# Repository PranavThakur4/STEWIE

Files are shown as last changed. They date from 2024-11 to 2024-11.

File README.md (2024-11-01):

# STEWIE
 Theuseofparallelmanipulatorsinaerospaceengineeringhasgainedsignificantattentiondueto
 their ability to provide improved stability and precision. This paper presents the design, control, and analysis
 of “STEWIE”,whichisathree-degree-of-freedom(DoF)parallel manipulator robot developed by members
 of the thrustMIT rocketry team, as a payload stabilization mechanism for their sounding rocket, ’Altair’. The
 goal of the robot was to demonstrate the attitude control of the parallel plate against the continuous change
 in orientation experienced by the rocket during its flight, stabilizing the payloads. At the same time, the high
 gravitational forces (G-forces) and vibrations experienced by the sounding rocket are counteracted. A novel
 design of the mechanism, inspired by a standard Stewart platform, is proposed which was down-scaled to
 fit inside a 4U CubeSat within its space constraints. The robot uses three micro servo motors to actuate the
 links that control the alignment of the parallel plate. In addition to the actuation mechanism, a robust control
 system for its manipulation was developed for the robot. The robot represents a significant advancement
 in the field of space robotics in the aerospace industry by demonstrating the successful implementation of
 complex robotic mechanisms in small, confined spaces such as CubeSats, which are standard form factors
 for large payloads in the aerospace industry.

 Stewie Payload
 STEWIE Cubesat 4U

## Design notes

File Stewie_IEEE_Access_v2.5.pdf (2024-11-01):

Date of publication xxxx 00, 0000, date of current version xxxx 00, 0000.

Digital Object Identifier 10.1109/ACCESS.2023.0322000

# Design and control of "STEWIE", a robotic payload stabilization mechanism for rocket flights

Utkarsh Anand¹* | Diya Parekh²* | Thakur Pranav G. Singh³* | Hrishikesh S. Yadav⁴
| Ramya S.
Moorthy⁵

| Srinivas G.⁶

1Department of Electrical & Electronics Engg., Manipal Institute of Technology, Karnataka, India - 576104 (email: utkarshanan221@gmail.com) 2Department of Mechatronics Engg., Manipal Institute of Technology, Karnataka, India - 576104 (email:diyaparekh0603@gmail.com) 3Department of Mechanical Engg., Manipal Institute of Technology, Karnataka, India - 576104 (email:thakur4pranav@gmail.com)
4Department of Data Science Engg., Manipal Institute of Technology, Karnataka, India - 576104 (email: yadavhrishikeshsingh@gmail.com) 5Department of Mechatronics Engg., Manipal Institute of Technology, Karnataka, India - 576104 (email: ramya.moorthy@manipal.edu) 6Department of Aeronautical & Automobile Engg., Manipal Institute of Technology, Karnataka, India - 576104 (email:srinivas.g@manipal.edu)

Corresponding author: Srinivas G. (e-mail: srinivas.g@manipal.edu).

*These authors share equal contribution
Project funded by Manipal Academy of Higher Education (MAHE) and undertaken by authors as members of thrustMIT Rocketry Team.

ABSTRACT The use of parallel manipulators in aerospace engineering has gained significant attention due to their ability to provide improved stability and precision. This paper presents the design, control, and analysis of “ STEWIE ”, which is a three-degree-of-freedom (DoF) parallel manipulator robot developed by members of the thrustMIT rocketry team, as a payload stabilization mechanism for their sounding rocket, ’Altair’. The goal of the robot was to demonstrate the attitude control of the parallel plate against the continuous change in orientation experienced by the rocket during its flight, stabilizing the payloads. At the same time, the high gravitational forces (G-forces) and vibrations experienced by the sounding rocket are counteracted. A novel design of the mechanism, inspired by a standard Stewart platform, is proposed which was down-scaled to fit inside a 4U CubeSat within its space constraints. The robot uses three micro servo motors to actuate the links that control the alignment of the parallel plate. In addition to the actuation mechanism, a robust control system for its manipulation was developed for the robot. The robot represents a significant advancement in the field of space robotics in the aerospace industry by demonstrating the successful implementation of complex robotic mechanisms in small, confined spaces such as CubeSats, which are standard form factors for large payloads in the aerospace industry.

INDEX TERMS Parallel Manipulators, Robotics, Payload, Sounding Rocket, Control Systems, Kinematics

I. INTRODUCTION
T

HE successful use of payloads in space missions depends largely on ensuring their stability and orientation control during the launch and spaceflight phases. Vibration motion, G-forces and dynamic disturbances caused by the rocket’s orientation during flight path can affect the integrity and functionality of the payload. To address these challenges, parallel manipulators have emerged as a promising solution, offering the potential to counteract these external perturbations and maintain precise alignment.
The inspiration for the design of our robot STEWIE comes from the versatility and robustness of the six degrees-of-freedom (DoF) Stewart platform, which is widely used in various industrial and research applications. Our research aims to take advantage of the principles of the Stewart platform while simplifying the kinematic structure to create a three-degrees-of-freedom (DoF) parallel manipulator suitable for payload stabilization in thrustMIT’s sounding rocket: Altair.
The main goal of this article is to present a comprehensive study of STEWIE’s design, development and performance characteristics. We address the kinematic analysis of the manipulator and illustrate its ability to provide three degrees-of-freedom for precise positioning of the payload during rocket ascent and spaceflight. In addition, we are investigating the integration of different types of joints and micro-servo motors into STEWIE’s structure to improve its parallel alignment with respect to the Earth’s surface. We present the results of the various structural simulations carried out on STEWIE to ensure that it can function effectively in the harsh conditions it will experience during its flight inside the rocket.
We also propose a computationally in-expensive but robust controller which has high response speeds and high movement accuracy.
The research results show that STEWIE has exceptional
VOLUME 11, 2023 | 1

Author et al.: Preparation of Papers for IEEE TRANSACTIONS and JOURNALS

potential as an effective payload stabilization system for sounding rockets such as Altair. The ability of the manipulator to actively counteract vibrational movements, G-forces and orientation changes ensures the integrity and reliable functionality of payloads during critical phases of space missions. Furthermore, its compact, lightweight and simple design contributes to the rocket’s overall efficiency and improved payload capacity.

A. CONTRIBUTIONS OF RESEARCH
The main contributions of this paper to the field of robotics and aerospace are the following:-
- A novel low-complexity, pwm-controlled actuator based payload stabilization mechanism for rocket flights.
- A computationally lightweight controller, demonstrating high accuracy and response time for critical robotic application especially in space industries.
- A simple and robust custom tuning method for pidcontrollers.
- An open-source platform comprising mechanical design files (STEP format), details of electronic components, and real-time-operating-system (RTOS).
B. ORANISATION OF PAPER
The paper is organized as follows: a comprehensive study on related work and recent development in the the field of robotics, especially for aerospace applications and in payloads has been presented in section II. The design of the robot detailing its geometry, kinematics involved, various components used, actuation mechanism, along with communication interfaces, sensors and circuitry design are described in section III. A detailed description of the control architecture including the controllers used, are explained in section IV. A comprehensive description of the tuning methods for the controllers is given in section V. Analysis of the simulations, and actual rocket flight results are presented in section VI. Finally, we present our conclusion in section VII.

II. RELATED WORK & RECENT DEVELOPMENTS
The utilization of Stewart platforms in aerospace applications has seen a surge in interest owing to their capability to provide precise control and stabilization in dynamic environments. Recent advancements in this field have seen various applications ranging from vibration control systems to robotic manipulators designed specifically for space missions. This section reviews significant advancements in the fields of robotics, Stewart platforms, and their application within the aerospace industry, focusing on the stabilization of payloads during rocket flights.
Stewart platforms, first introduced by Eric V. Gough (1947)
[2] and D.Stewart et al. (1965) [1] are known for their high stiffness, force capabilities, and precise motion control and have been increasingly employed in aerospace applications to address challenges related to maintaining orientation and stability in dynamic environments. Research by Tsai et al. (1999) [3] and Melek et al. (2010) [4] have highlighted the mechanics and kinematics of Stewart platforms, emphasizing their suitability for tasks requiring high precision and complex motion control.
Wang et al. (2022) [7] explored the utilization of Stewart platforms in the low-frequency vibration characteristic testing of space truss deployable antennas mounted on satellites. Their study demonstrated the effectiveness of Stewart platforms in conducting vibration tests, crucial for assessing the structural integrity and performance of satellite components in space environments.
Preumont et al. (2007) [6] presented a pioneering work on a six-axis single-stage active vibration isolator based on a Stewart platform. This work introduced a novel approach to mitigating vibrations in aerospace systems, which is essential for improving the accuracy and reliability of sensitive instruments and payloads onboard spacecraft.
Liang et al. (2021) [5] contributed to the field with their research on the design and implementation of a high-precision Stewart platform tailored for a space camera. Their study focused on achieving precise positioning and stabilization of the camera platform, crucial for capturing high-quality images and conducting remote sensing operations in space. In a related study, Liang et al. (2022) conducted kinematics and dynamics simulations of a Stewart platform, providing valuable insights into its motion characteristics and performance metrics.
Furthermore, Glassner (2021) explored the concept of soft Stewart platforms tailored for robotic in-space assembly applications. This innovative approach introduces flexibility into the platform structure, enabling adaptability to varying task requirements and enhancing safety during assembly operations in space environments.
These works collectively highlight the diverse applications and recent advancements in Stewart platform technology within the aerospace industry. The versatility, precision, and adaptability of Stewart platforms make them indispensable for a wide range of aerospace missions, including satellite deployment, vibration control, payload stabilization, and in-space assembly operations.

III. ROBOT DESIGN
In this section we will discuss in detail the overall geometry of the mechanical structure, the forward kinematic calculations for the robot, the computing & communication implemented, finally focusing on the leg design and the actuation mechanism of the robot.
A. GEOMETRY OF ROBOT
The hardware design of STEWIE is inspired from a Stewart-Gough Platform [1]. The design philosophy behind the mechanism is based on compactness, light weight construction, ease of manufacturing, rapid repair and robust operation. The design of the robot can be understood as an assembly of three sections, stationary base & middle plates, 3 identical custom designed legs and a dynamic top plate where the payload to be stabilized sits (refer Fig. 1). STEWIE weighs
2 | VOLUME 11, 2023

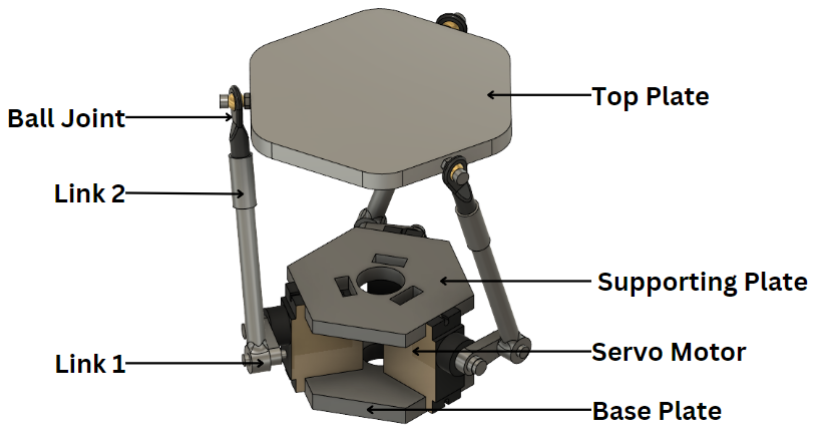
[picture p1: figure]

FIGURE 1. Computer Aided Design (CAD) of STEWIE Robot

TABLE 1. Physical Robot Parameters

Parameter | Symbol | Value | Units
Mass | m | 485 | g
Minimum Body Height | lbody | 110 | mm
Maximum Body Height | lbody | 125 | mm
Body Width | wbody | 85 | mm
Leg Link Length | l1, l2, l3 | 79 | mm
Maximum Load Capacity | - | 10.91 | kg-f

around 485 g with a maximum height of 125 mm, when fully extended and minimum height of 110 m, from ground to top plate depending on the positions of the legs. Each leg of the robot measures a total length of 79 mm and has a maximum load capacity of 10.91 kg − f .

Degrees of Freedom
The degrees-of-freedom of STEWIE were calculated using Chebychev–Grübler–Kutzbach criterion:

FT = 6(N − 1 − J) +X(Fi
- Ji) | (1)

Where,
N : Number of links = 8
J : Number of joints = 9
Fi

: Degrees of Freedom of a joint
Ji

: Number of joints with the same degree-of-freedom

Here, the summation term of (1) represents the effective constraints which are acting on the robot. In STEWIE, six revolute joints with one-degree-of-freedom and three ball joints with three-degrees-of-freedom each have been used. Hence, the summation term of (1) can be calculated as follows:

X(Fi · Ji) = (1 · 6) + (3 · 3) = 15

Therefore, on substituting the given values in the criterion given in (1), degrees-of-freedom calculated for STEWIE is calculated as FT = 3.

B. COMPUTING AND COMMUNICATION
The robot was deployed inside a CubeSat, which was divided into two segments. The upper segment houses the robot along with two first-person-view (FPV) cameras to record the movement of the plates during the rocket flight from two

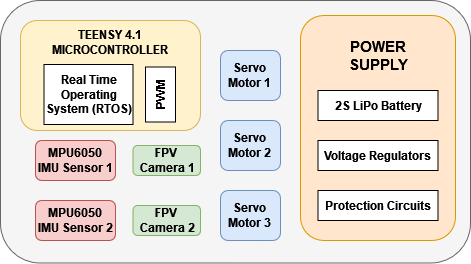
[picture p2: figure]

FIGURE 2. Electronics System Block Diagram

different angles. For inertial measurement, a small printedcircuit-board (PCB) is mounted on the top plate of the robot which has a MPU6050 inertial-measurement-unit (IMU) on it for orientation data of the plate. A secondary IMU is mounted on the bottom plate of the robot, which remains stationary with respect to the frame of reference of the rocket during its flight. This secondary IMU helps to determine the orientation of the top plate in reference to the rocket’s frame of reference. The bottom segment consists of majority of the electronics components, cable routing and two power distribution boards each for the two cameras. The power is supplied to the parallel manipulator robot through an extension from a 2S Lithium-Polymer (LiPo) battery with additional batteries for redundancy. The central processing unit of the robot is a Teensy 4.1 microcontroller, functioning on a FreeRTOS based real-timeoperating-system (RTOS). The processor communicates with the IMU sensor daughter boards through high-speed Inter-Integrated-Circuit (I2C) interface with each IMU sensor on a different address. The servo motors are controlled by the microcontroller via pulse-width-modulated (PWM) signals generated by it (refer Fig. 2). This setup executes control strategies, including control of motors at frequencies as high as 200 Hz.

C. LEG DESIGN & ACTUATION
The robot comprises of three legs. Each leg of the robot is divided into three sections. The bottom section of the leg is a revolute joint which comprises a micro-servo motor placed at the base of each leg and a link-1 (refer Fig. 3) which connects the motors to the middle section of the leg. Link-1 is connected to the middle section of the leg through a nutbolt mechanism, which acts as the second revolute joint. The middle section of the robot is a cylindrical rod which we call as Link-2 (refer Fig. 3). The top section of the leg comprises of a ball joint which connects the leg to the top plate of the robot. The motors are attached and sandwiched between the middle and the base plate of the robot to prevent them from moving during the actuation of the robot. The motor acts as the driver for the actuator and the joints above are driven by it, translating the motor’s rotary motion into linear and angular displacement of the top plate. Each leg of the robot measures a total length of 79 mm and weights around 26 g.

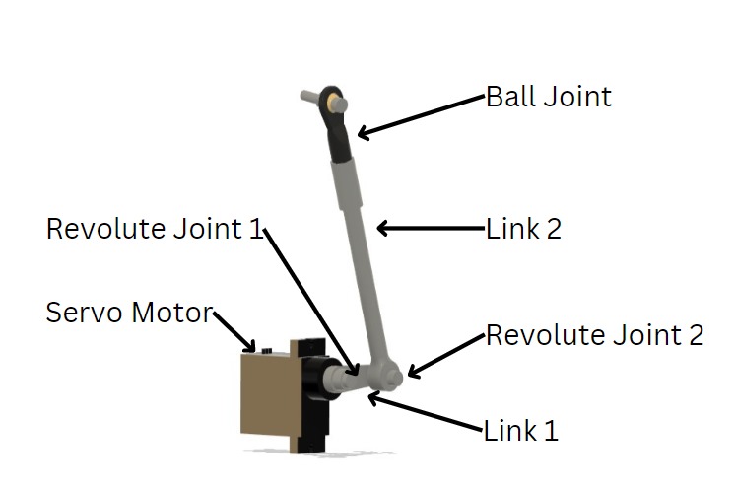
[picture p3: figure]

FIGURE 3. Leg Design of Robot

During development of the robot, other potential methods of actuation were also explored such as pneumatic actuators, linear actuators in its early iterations. Though effective, but these early iterations were rejected due to unavailability of cost effective commercial actuators and space constraints inside the CubeSat.

TABLE 2. Specification of Components of Robot

Part | Material | Weight | Units
Top Plate | ABS Plastic | 53 | g
Middle Plate | Steel | 105 | g
Base Plate | Steel | 85 | g
Link 1 | Aluminium 6061 | 13 | g
Link 2 | Aluminium 6061 | 4 | g
Ball Joint | Plastic | 3 | g

TABLE 3. Micro Servo Motor Specifications

Parameter | Value | Units
Model | SG-90
Mass | 9.0 | g
Motor Size | 22.2 | mm
| 11.8 | mm
Operating Speed | 0.1 | s/60 degree
Operating Voltage | 4.8 | V
Maximum Torque | 2.5 | Kg-cm

IV. CONTROL ARCHITECTURE
Our control architecture follows a combination of a custom robot state estimator which analyzes the orientation of the robot’s top plate along the {X, Y , Z} axes and performs forward kinematic calculations to determine the position matrix of the ball joints in the form of cartesian coordinates in the three-dimensional space, which is then passed as an input to three separate low-level controllers for each of the three legs (refer Fig. 6). The controllers generates the motor angles for each motor, by which the it should move to ensure that the top plate is parallel to the ground no matter the orientation of the

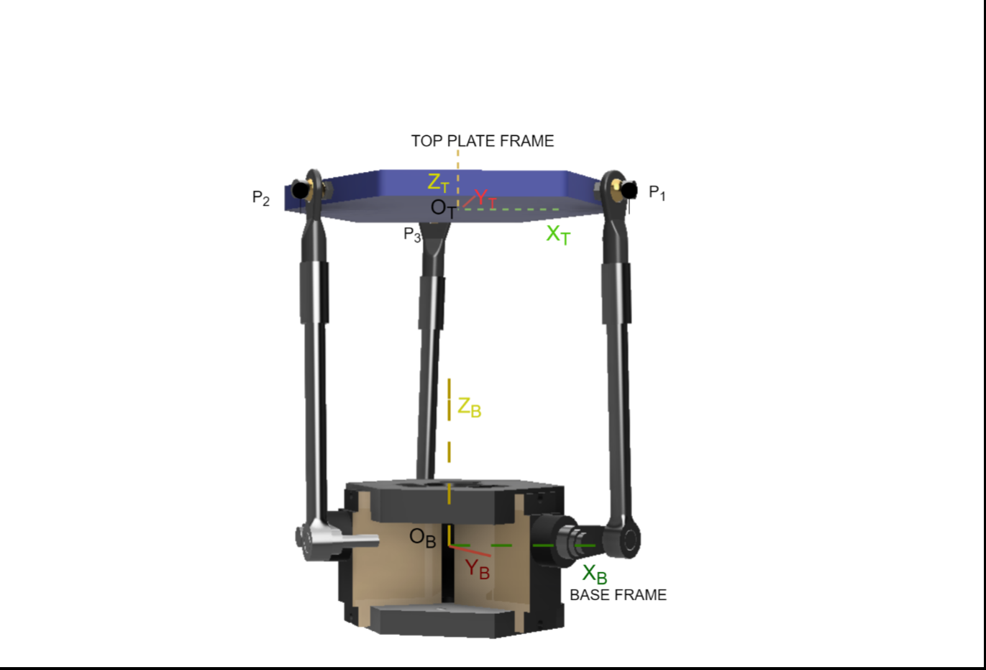
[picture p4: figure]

FIGURE 4. Frame of References in Robot

robot or the rocket. This in-turn stabilizes the payload which is kept on the robot.
This control approach allows for a decoupling of the control process, simplifying the design and implementation.
A. ROBOT STATE ESTIMATOR
Robot’s State: The state of the robot at any given time, is a three-dimensional vector St = {Xp, Yp, Zp} consisting of the position coordinates of the ball joints with respect to the the base frame (refer Fig. 4) along the X, Y & Z axis at which the legs are connected to the plate through the ball joints. Forward Kinematic calculations were done on the robot to determine the final position matrix of the ball joints. The IMU sensor which is attached to the top plate of the robot has a three-axis gyroscope and can give orientation data of the top plate in the form of angle deviations from three axes as known as Yaw, Pitch and Roll. This information was utilized to calculate the position of ball joints in the base frame. Here, the ’base frame’ is defined as the initial frame located at the centre of the three motors (refer Fig. 4). The base frame is at a fixed distance from the frame of reference of the top plate throughout the flight irrespective of the position of the motors. Position matrix of top plate with-respect-to base plate frame of the robot was presented as BTT , where, {θX , θY , θZ } are the angle deviations of the top plate along from the X, Y , Z axes obtained from the Yaw-Pitch-Roll data from the IMU and BZT is the fixed distance between the top plate frame and base frame. The position matrix of ball joint with respect to top plate frame was represented as T TP, where, {x, y,z} are the coordinates of the ball joints in the three-dimensional space in the frame of reference of the top plate.
To find position matrix of ball joint with respect to base frame, BTT and T TP were multiplied.

BTP =

T TP ·

BTT | (2)

Refer to Fig. 5 for detailed matrix multiplications.

TTP =

1 0 0 x
0 1 0 y
0 0 1 z
0 0 0 1

BTT =

cos θZ · cos θY | − sin θZ · cos θX + cos θZ · sin θY · sin θX | sin θZ · sin θX + cos θZ · sin θY · cos θX | 0
sin θZ · cos θY | cos θZ · cos θX + sin θZ · sin θY · sin θX | − cos θZ · sin θX + sin θZ · sin θY · cos θX | 0
− sin θY | cos θY · sin θX | cos θY · cos θX | BZT
0 | 0 | 0 | 1

BTP =

cos θZ · cos θY | − sin θZ · cos θX + cos θZ · sin θY · sin θX | sin θZ · sin θX + cos θZ · sin θY · cos θX | Xp
sin θZ · cos θY | cos θZ · cos θX + sin θZ · sin θY · sin θX | − cos θZ · sin θX + sin θZ · sin θY · cos θX | Yp
− sin θY | cos θY · sin θX | cos θY · cos θX | Zp
0 | 0 | 0 | 1

FIGURE 5. Position Matrices of Robot

Where,
Xp = (cos θZ · cos θY ) · x + (− sin θZ · cos θX + cos θZ · sin θY · sin θX ) · y + (sin θZ · sin θX + cos θZ · sin θY · cos θX ) · z Yp = (sin θZ · cos θY ) · x + (cos θZ · cos θX + sin θZ · sin θY · sin θX ) · y + (− cos θZ · sin θX + sin θZ · sin θY · cos θX ) · z Zp = (− sin θY ) · x + (cos θY · sin θX ) · y + (cos θY · cos θX ) · z + Z

B
T

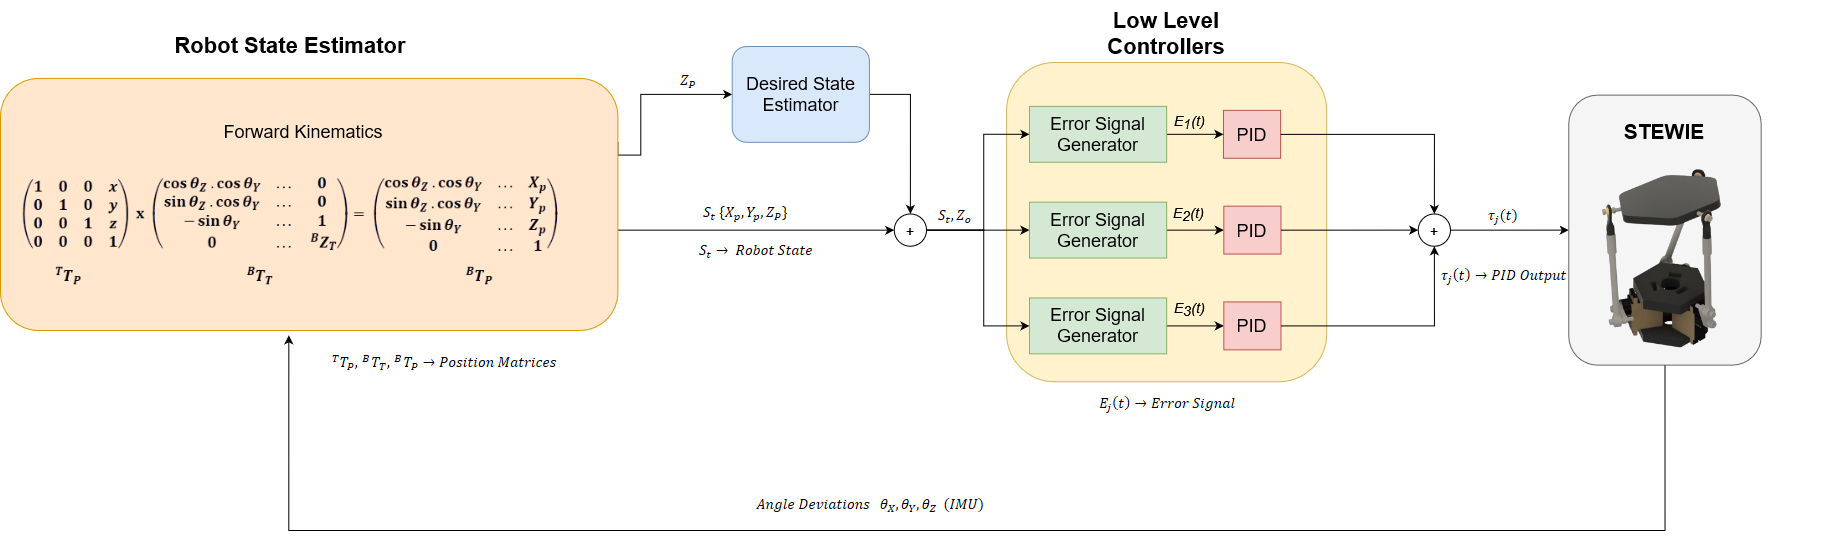
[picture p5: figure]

FIGURE 6. Control Architecture

B. LOW LEVEL CONTROLLER

Approaching the robot’s locomotion challenge from a control theory perspective, we aim to develop a policy capable of parameterizing the relationship between the angular positions of the servo motors and the orientation of robot’s top plate in the three-dimensional space furthermore analyzing how changing the angular position of the servo changes the orientation of the top plate. These parameterized value act as inputs for the controllers, which, in turn, incorporates a regulatory mechanism based on the orientation state of each leg.

Desired State: The desired state of the robot is one in which the top plate should be parallel to the ground. In our case, when the top plate is parallel to the ground, it is in absolute horizontal orientation with respect to the ground surface and at that instance, the z−coordinate of all the ball joints are same. Therefore, the controller will be regulating the motors such that their z−coordinate of all the motors are same to achieve horizontal orientation of the top plate with respect to ground.

Error Signal: At any given state, the errors signal (Ej) for the three controllers are calculated by taking the absolute difference between between the desired z-coordinate, Zo, also known as set-point (SP) and the actual z-coordinates of the three points of the ball joints, Zp1

, Zp2

, Zp3
, also known as
process-variables (PV) in control theory.

Ej = |Zo − Zpj

| ∀ j = 1, 2, 3 | (3)

The desired z-coordinate (Zo) for the controller is chosen as the median of the actual z-coordinates of the three ball joints.

Zo = median{Zp1
, Zp2

, Zp3

} | (4)

This also reduces the computational complexity of the model as, at given state, controller calculations for only two of three motors have to be done because the leg having the median z-coordinate will remain stationary.
The motor level controllers tracks the z-coordinates of the plate points at every time instant ’t’ using a Proportional-Integral-Derivative (PID) controller with appropriate gains Kp, Ki

, and Kd for each of the three controllers as follows:

τj(t) = Kpj

- Ej(t) + Kij

·

Xt−1

k=0

Ej(k) + Kd · E˙
j(t)

∀ j = 1, 2, 3 (5)

Where,
τtj
: PID output of the j

th controller at time instant t. Etj

: Error of the j

th controller at time instant t. Ref. (3) Kpj

: Proportional gain of the j

th controller.
Kij

: Integral gain of the j

th controller.
Kdj

: Derivative gain of the j

th controller.

V. TUNING OF CONTROLLERS
The effective tuning of PID controllers is crucial for achieving optimal performance in robotic system, particularly those with complex dynamics such as parallel manipulators. In this section, we will discuss the methods employed for tuning the PID controllers. We utilized three different methods: a custom tuning method and two heuristic tuning methods, Ziegler-Nicholas, proposed by J.G. Ziegler & N.B. Nicholas (1942)
[13] and the Cohen-Coon Method, proposed by G.H. Cohen and G.A. Coon (1953) [14].
In all the methods, to get system response signal, the process-variable which are the z-coordinates Zp1

, Zp2

, Zp3
for
the three ball joints and set-point, which is the desired z-coordinate Zo; were plotted against time t. Final values of PID gains were chosen based on the comparison results of the different methods.
A. CUSTOM TUNING METHOD
This method was an modified version of the trial-error method of tuning a controller. The method involved performing open-loop test on the controller to determine the process characteristics of the controller followed by manually adjusting the gains depending on the results of the open-loop test. We used a random value of the set-point during each iteration as the reference signal.
The process involved following steps:
1) Perform Open-loop Test
The controllers were configured in manual mode and a stepchange was introduced as the output signal. The process-variable (PV) curve response was monitored continuously and it was determine the that controller gave a self-regulating characteristic with pure 1

st order lag. Hence, it was inferred that the proportional gain was dominant for the controller had to be aggressive along with a nominal integral gain. The derivative gain could be used or avoided depending on the results in the future.

2) Manually Adjusting Gains
After recognising the characteristics of the controller, the gains were initialized with values of Kp & Ki = 0.5 and Kd = 0. Post initialization, they are manually adjusted based on rules given in Table 4 to achieve the best compromise between stability and quick response of the system.
B. ZIEGLER-NICHOLS METHOD (CLOSED LOOP) Ziegler-Nicholas closed-loop is a heuristic method for tuning controllers in which certain parameters of the system such as Ultimate Gain (Ku) and Critical Period (τu) are determined manually through experimentation. Following which, the Kp, Ki

, Kd gains can be calculated through pre-determined rules based on the ultimate gain and the critical period given in Table 5.

TABLE 5. Ziegler-Nicholas Method Tuning Rule

Gain Type | Kp | Ti | Ki | Td | Kd
P | Ku/2 | - | - | - | -
PI | Ku/2.2 | τu/1.2 | Kp/Ti | - | -
PID | Ku/1.7 | τu/2 | Kp/Ti | τu/8 | Kp ∗ Td

The process involved the following steps:
Step 1 : Keeping the integral gain (Ki) and derivative gain (Kd ) as zero, proportional gain (Kp) is increased until the system starts to oscillate continuously at a constant amplitude. The gain at this point is called the Ultimate Gain (Ku). The calculated values of ultimate gains for the three controllers is given in Table 6.
Step 2 : Critical Period (τu) is determined by measuring the period of oscillation at the ultimate gain. The calculated values of critical periods for the three controllers is given in Table 6.
Step 3 : Using a set of pre-defined formulas presented by Ziegler-Nicholas given in Table 5, the values of

TABLE 4. General rule for tuning control parameters

Parameter | Rise Time | Overshoot | Settling Time | Steady-State Error
Kp | Decrease | Increase | Minor Change | Decrease
Ki | Decrease | Increase | Increase | Eliminate
Kd | Minor Change | Decrease | Decrease | Minor Change

Kp, Ki

, Kd gain were calculated. Final values of the gains are given in Table 6.

TABLE 6. Gains calculated through Ziegler-Nicholas Method

Type of Controller | Ku | τu | Kp | Ti | Td
Leg 1 PID Controller | 6.63 | 0.24 | 3.98 | 0.12 | 0.03
Leg 2 PID Controller | 4.65 | 0.24 | 2.79 | 0.10 | 0.03
Leg 3 PID Controller | 7.92 | 0.16 | 4.75 | 0.08 | 0.02
C. COHEN-COON METHOD
Cohen-Coon method is an extension of the Ziegler-Nicholas Method, but uses more information from the system in the process. The system’s response is modelled to a step change as a first-order response plus dead time using this method. From the response, three parameters: K, τm and τd are founded. K is the output steady state divided by the input step change, τm is the effective time constant of the first-order response, and τd is the dead time.

τm =

3
2
(t2 − t1) | (6)
τd = t2 − τm | (7)

To verify the results, according the Cohen Coon rules, the dead time should be less than two times the length of the time constant [1]. The Cohen Coon relations for calculating the PID gains is given in Table 7.

TABLE 7. Cohen-Coon Method Tuning Relations

Type of Controller | Kp | Ti | Td
P | τm (1 + τd ) Kτd 3τm | - | -
PI | τm (0.9 + τd ) Kτd 12τm | 30+3τd/τm τd ( ) 9+20τd/τm | -
PD | τm (1.25 + τd ) Kτd 6τm | - | 6−2τd/τm τd ( ) 22+3τd/τm
PID | (1 + τd τm ) Kτd 3τm | 32+6τd/τm τd ( ) 13+8τd/τm | τd ( 4 ) 11+2τd/τm

The obtained system parameters and calculated systems gains are given in Table 8.

TABLE 8. System parameters calculated through Cohen-Coon Method

Controller | K | τd | τm | Kp | Ti | Td
Leg 1 PID Controller | 2.9 | 0.07 | 0.47 | 2.85 | 0.43 | 0.08
Leg 2 PID Controller | 3.92 | 0.03 | 0.37 | 2.15 | 0.25 | 0.06
Leg 3 PID Controller | 1.71 | 0.05 | 0.55 | 4.58 | 0.55 | 0.05

The system response curves for tuning PID controllers using the above given methods is given in Fig. 7.

VI. RESULTS & DISCUSSIONS
A. SIMULATIONS
1) Modal Analysis
Necessary modal analysis simulation was performed on the robot to observe its behaviour under high vibrational forces. The formations and stress zones were identified at different natural frequencies and accordingly the design of the robot was also modified to provide more support in high stress areas. Based on the analysis, the robot was finally designed to sustain a maximum of 16 G-forces under continuous orientation change during the rocket flight.
The simulations were performed for five mode shape results for a total deformation. As expected, the maximum stress was found to be at the joints in the link-2 and the ball joint as they were externally joined by a transition fit but sufficient length was not present to hold on. Stress regions were also observed at the sharp edges of the top plate and the link-2, which weren’t filleted to reduce stress concentration. However, the edges were filled and filleted later to least possible diameter to justify the stress concentration. The maximum total deformation observed was 261.57 mm at a frequency of 761.13 Hz. Since, the natural frequency of the rocket during its flight was between 70 - 100 Hz, we were in a safe zone with a decent amount of factor of safety.
2) Static Structural Simulation
It was necessary to perform static structural simulations on the robot to observe the effects of downward acting load on the robot, experienced during the rocket flight. To carry out the simulations, the 3D CAD model was imported into the Ansys software as a STEP file. Appropriate materials were assigned to the respective parts of the robot and the

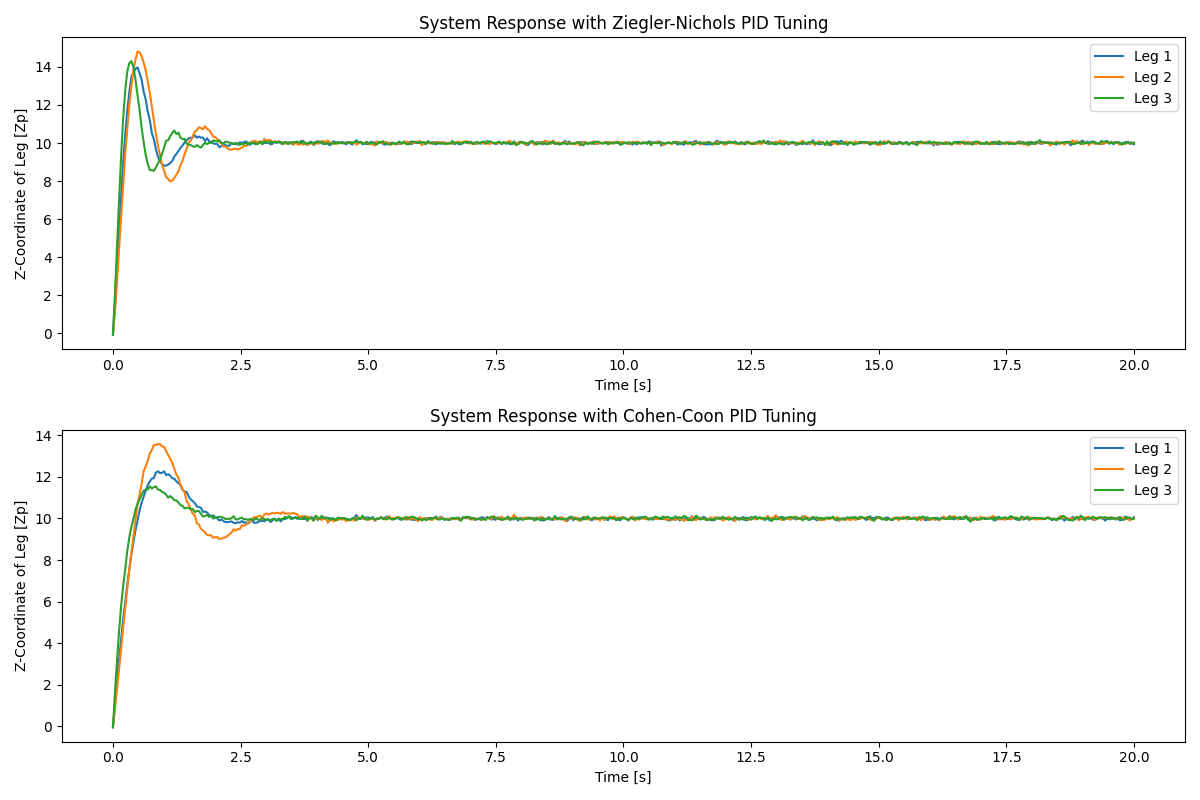
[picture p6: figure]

FIGURE 7. System Response Curves for PID Controllers with desired Zo = 10

necessary regions were given the property of contact regions bonded with no separation. To define the threads region, local coordinate system was assigned to the center of the bolts. Further, meshing was performed to the model, which was a combination of Tet and Hex mesh elements. The regions where the load effects were anticipated to be higher like the links, Hex mesh was assigned to such regions for accurate results and the regions where the loads were anticipated to be lesser, Tet mesh was assigned to reduce overall complexity and compute time of the simulation. There were a total of 0.25 million elements in quadratic order with a size of 0.75 mm.
The force applied to the simulation was calculated as following:- The maximum torque which can be delivered by the servo motor was 10g/cm or 1kg/m. The length of each link was 15 mm, hence through simple torque calculation, the maximum force on each link was 66.66 N in the ideal condition. Considering losses and practical efficiency of 85% for the motors, the maximum force on each link can be calculated as 56N or 5.6Kg. Adding a factor of safety of 1.5 for maximum load, each link could lift a maximum weight of 3.8Kgs, therefore making it 11.4Kgs for the whole robot which converts to approximately, 107N.
During the rocket’s flight, the maximum downward G-forces acting on the rocket was 12G’s which is equivalent to 117N. Majority of this downward force is experienced by the frame and the structure of the rocket body namely the stringers and the bulkheads. The payload is also protected by its own supporting plates and the walls of the CubeSat. Thus, the net effect of these downward forces acting on the payload is significantly reduced, approximately up to 50% of its original value.

Therefore, final value of the G-force acting on the payload is considered as 59N. The weight of the top plate was itself 5N and the weight of the payload which was kept on the top plate to be balanced was 6N. Adding all these forces gives a total of 70N of acting in the downward direction, which is well below the maximum weight that the links can handle.

For simulation purposes, the maximum value of down force was considered and applied at the centre of the top plate, the fixed support at the bolt holes and the base plates. Displacement support to the ball joints were also added. Simulations were done for total deformation and equivalent stress to locate the high stress regions. The maximum deformations of 4.098e-4 mm were observed at the edges of the top plate, where there were no bolt holes. The maximum equivalent stress of 6.637 MPa was observed at the points where the ball joints were attached to the top plates.

Observing these results, we concluded that there was no major concern regarding the design as every parameters was within the expected range even with aspect ratio being only
7. The simulation proved the design’s load bearing capacity.
B. ROCKET FLIGHT RESULTS
The robot was launched on an actual sounding rocket for testing. Throughout the operation of the robot, the IMU data was being logged onto an external SD Card by the microcontroller. Post rocket flight, the data was accessed, processed and cleaned for analysis. The Yaw-Pitch-Roll data obtained from the SD Card is presented in Fig. 8. The data concludes that the top plate of the robot remained almost horizontal with respect to the ground throughout the rocket flight and the angle deviations from the absolute zero degrees were minimum.

VII. CONCLUSIONS
The development and implementation of the STEWIE payload stabilization mechanism represent a significant advancement in the field of aerospace engineering. This research has demonstrated the feasibility and effectiveness of using a three-degree-of-freedom (DoF) parallel manipulator for maintaining the stability and orientation of payloads during rocket flights. The design, inspired by the Stewart platform, successfully addressed the challenges posed by high

G-forces, vibrations, and dynamic disturbances experienced during rocket ascents.
Extensive simulations and analyses were conducted to evaluate the robot’s performance and robustness in dynamic environments. Modal analysis and static structural simulations confirmed the design’s ability to withstand up to 16-G forces during continuous orientation changes. Rocket flight tests validated the effectiveness of the control system, with the top plate maintaining near-horizontal alignment throughout the flight.
Our results indicate that STEWIE’s novel low-complexity, PWM-controlled actuator and lightweight control system provide exceptional precision and responsiveness, crucial for space applications. The robust performance of STEWIE in various simulations and actual flight tests confirms its potential to enhance payload stability, ensuring the integrity and functionality of critical instruments during missions.
The compact and lightweight design of STEWIE also contributes to the overall efficiency of the rocket, allowing for improved payload capacity without compromising performance. This research paves the way for future innovations in payload stabilization mechanisms, suggesting that similar systems can be adapted for a variety of aerospace applications, including CubeSats and other small-scale payloads.
Future research directions include exploring the use of ad-

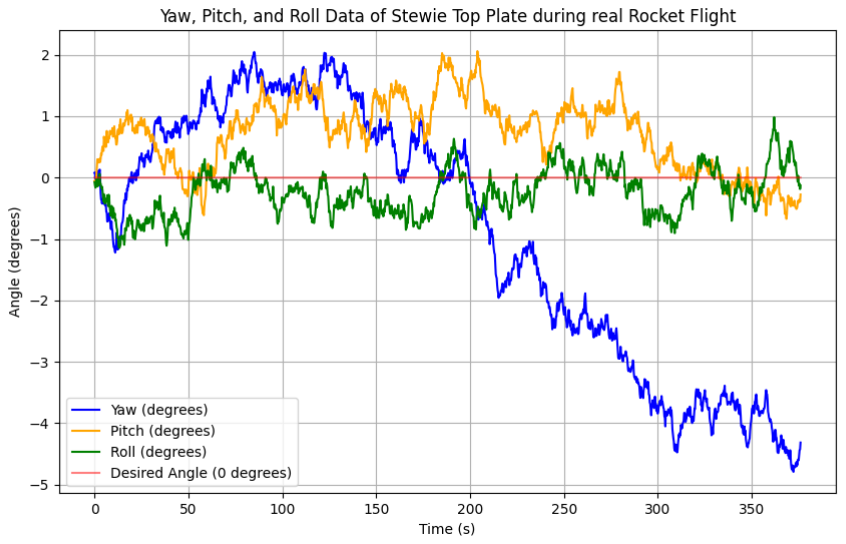
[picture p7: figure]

FIGURE 8. Yaw - Pitch - Roll data gathered from IMU sensor

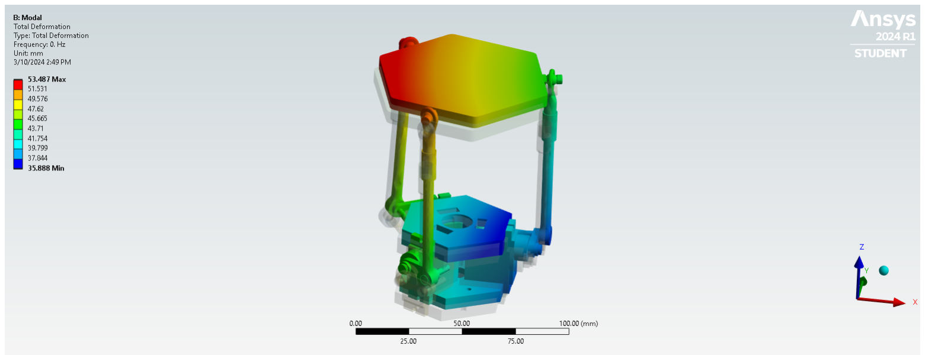
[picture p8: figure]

FIGURE 9. Modal Analysis Total Deformation 1

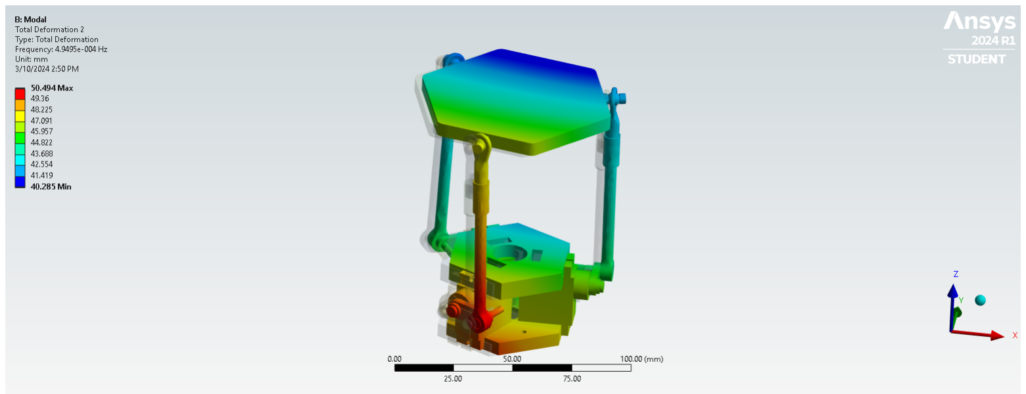
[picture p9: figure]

FIGURE 10. Modal Analysis Total Deformation 2

vanced materials, optimizing the kinematic structure, and investigating the integration of additional sensors for enhanced control and monitoring capabilities.
In conclusion, STEWIE exemplifies the integration of advanced robotics and control systems in aerospace engineering, providing a reliable solution for payload stabilization in dynamic and harsh environments. Future work will focus on further refining the design, exploring the use of alternative materials and actuation methods, and expanding the application of this technology to other types of space missions.

ACKNOWLEDGEMENT
We sincerely thank thrustMIT, Manipal Institute of Technology, and the Manipal Academy of Higher Education for their invaluable support and resources that greatly facilitated the successful completion of this research.

REFERENCES

[1] D. Stewart, “A Platform with Six Degrees of Freedom,” Proceedings of the Institution of Mechanical Engineers, vol. 180, no. 1, pp. 371–386, Jun. 1965.
[2] V. E. Gough and S. G. Whitehall, ‘Universal Tyre Test Machine,’ Proceedings of 9th International Congress FISITA, May 1962, pp. 117-137
- References - Scientific Research Publishing.
[3] L. W. Tsai, "The Mechanics of Serial and Parallel Manipulators," Wiley-Interscience, 1999.
[4] W. W. Melek and A. A. Goldenberg, “Neurofuzzy control of
modular | and | reconfigurable | robots,” | IEEE/ASME | Transactions
on Mechatronics, vol. 8, no. 3, pp. 381–389, Sep. 2003, doi: https://doi.org/10.1109/tmech.2003.816802. .
[5] F. Liang, S. Tan, J. Fan, Z. Lin, and X. Kang, “Design and Implementation of a High Precision Stewart Platform for a Space Camera,” Journal of Physics: Conference Series, vol. 2101, no. 1, p. 012015, Nov. 2021, doi: https://doi.org/10.1088/1742-6596/2101/1/012015. .

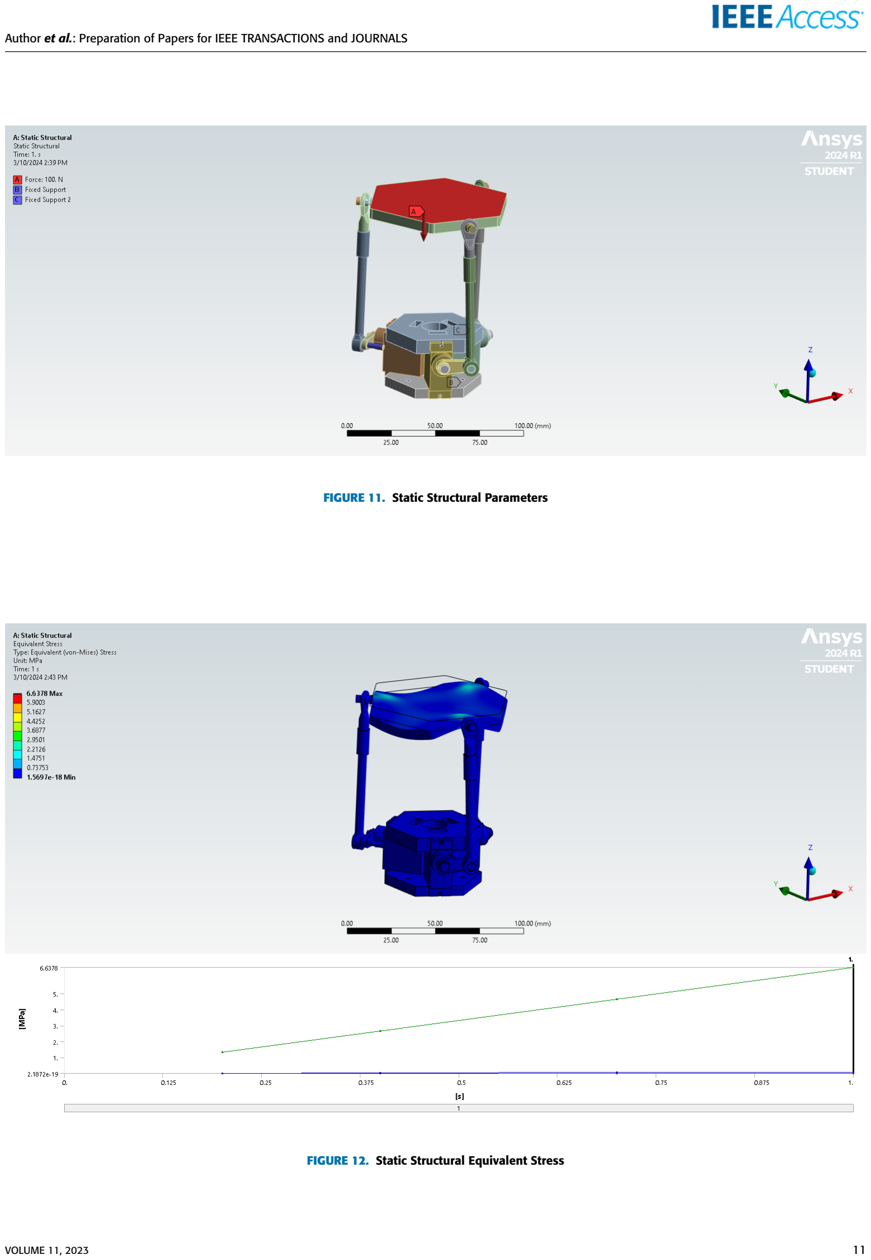
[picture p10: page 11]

FIGURE 11. Static Structural Parameters

FIGURE 12. Static Structural Equivalent Stress

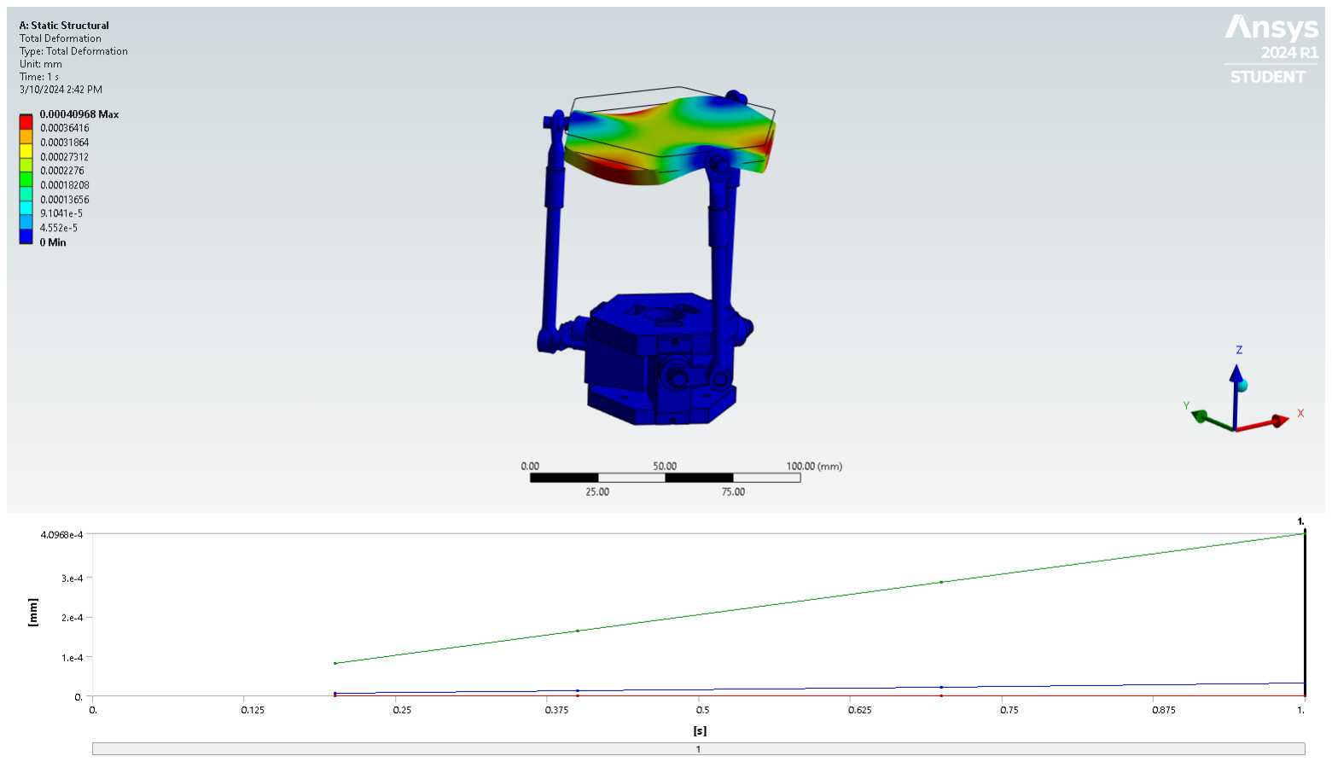
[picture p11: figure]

FIGURE 13. Static Structural Total Deformation

[6] Bruno De Marneffe, M. Avraam, Arnaud Deraemaeker, Mihăiţă Horodincă, and André Preumont, “Vibration Isolation of Precision Payloads: A Six-Axis Electromagnetic Relaxation Isolator,” Journal of Guidance Control and Dynamics, vol. 32, no. 2, pp. 395–401, Mar. 2009, doi: https://doi.org/10.2514/1.39414. .
[7] H. Wang, J. Zhao, Y. Xue, Z. Huang, S. Zheng, and X. Ma, “Application of Stewart Platform in the Low-Frequency Vibration Characteristic Test of Space Truss Deployable Antenna on Satellite,” International Journal of Aerospace Engineering, vol. 2022, pp. 1–8, Jul. 2022, doi: https://doi.org/10.1155/2022/8063786. .
[8] Vigen Arakelian, Sébastien Briot, S. Jatsun, A. Jatsun. A New 3-DoF Planar Parallel Manipulator with Unlimited Rotation Capability. 13th World Congress in Mechanism and Machine Science, Jun 2011, Guanajuato, Mexico. ffhal-00553092f.
[9] Himam Saheb Shaik and G. Satish Babu, “Kinematic Performance Analysis of 3-DOF 3RRR Planar Parallel Manipulator,” Advances in intelligent systems and computing, pp. 879–894, Jan. 2021. .
[10] C. C. Nguyen, S. S. Antrazi, Z.-L. Zhou, and C. E. Campbell, “Adaptive control of a stewart platform-based manipulator,” Journal of Robotic Systems, vol. 10, no. 5, pp. 657–687, Jul. 1993, doi: https://doi.org/10.1002/rob.4620100507. .
[11] W. Chi, H. Ma, C. Wang, and T. Zhao, “Research on Control of Stewart Platform Integrating Small Attitude Maneuver and Vibration Isolation for High-Precision Payloads on Spacecraft,” Aerospace, vol. 8, no. 11, pp. 333–333, Nov. 2021, doi: https://doi.org/10.3390/aerospace8110333.
[12] B. Ding, B. S. Cazzolato, S. Grainger, R. M. Stanley, and J. J. Costi, “Active preload control of a redundantly actuated Stewart platform for backlash prevention,” May 2013, doi: https://doi.org/10.1109/icra.2013.6630830.
[13] J. G. Ziegler and N. B. Nichols, “Optimum Settings for Automatic Controllers,” Journal of Fluids Engineering, vol. 64, no. 8, pp. 759–765, Nov. 1942, doi: https://doi.org/10.1115/1.4019264.
[14] G. H. Cohen and G. A. Coon, “Theoretical Consideration of Retarded Control,” Journal of Fluids Engineering, vol. 75, no. 5, pp. 827–834, Jul. 1953, doi: https://doi.org/10.1115/1.4015451.

UTKARSH ANAND is a senior undergraduate pursuing his B.Tech in Electrical and Electronics Engineering from Manipal Institute of Technology, Karnataka, India, graduating in 2024.
From 2021 to 2023, he was member of the thrustMIT student rocketry team as Head of the Payload division and Launch Operations Lead for the team. Apart from payloads, he has also worked on developing novel deployment mechanism for payloads in sounding rockets as well as Deep Learning based control mechanisms for optimized control of airbrakes in the rocket. Between 2022 and 2023, he has also worked as a Research Interns at several other prestigious institutions such as Indian Institute of Sciences (IISc), Indian Institute of Technology Roorkee (IITR) and Defence Research & Development Organization (DRDO). His research interests include legged robotics, controller design for robotic applications in space and reinforcement learning.
Mr. Utkarsh Anand was a recipient of the prestigious IASc-INSA-NASI Summer Research Fellowship by Indian Academy of Sciences in 2022. He was a member of Association of Computing Machinery (ACM) from 2022 to 2023.

DIYA PAREKH is a senior undergraduate pursuing her B.Tech in Mechatronics Engineering from Manipal Institute of Technology, Karnataka, India, graduating in 2024.
From 2021 to 2023, she was a member of Payload division at thustMIT student rocketry team, a constituent of Manipal Academy of Higher Education. She has also worked on other projects like Direct Air Capture(DAC) in payload. Apart from developing payloads, she has also worked several other projects such as Automated drilling machine, pick and place pneumatic arm, automatic dam shutter control system, soft gripper. Her research interests include design, kinematics and control of robots

THAKUR PRANAV G. SINGH is senior undergraduate, pursuing B.Tech in Mechanical Engineering from Manipal Institute of Technology, Karnataka, India, graduating in 2024.

From 2021 to 2023, he was a senior member of Payload and Structures division at the thrustMIT student rocketry team, a constituent of Manipal Academy of Higher Education. In 2023, he worked as an intern at the prestigious Defence Research and Development Laboratory (DRDL) a laboratory of Defence Research and Development Organization (DRDO), working on projects to develop a micro thrust stand to support micro-thrusters and to develop a pressure regulator for the same. He has earlier worked on projects like spectroscopy, Carbon Nano Tubes(CNT), Direct Air Capture (DAC) in payload and designing of a Radial deployment mechanism in sounding rockets.

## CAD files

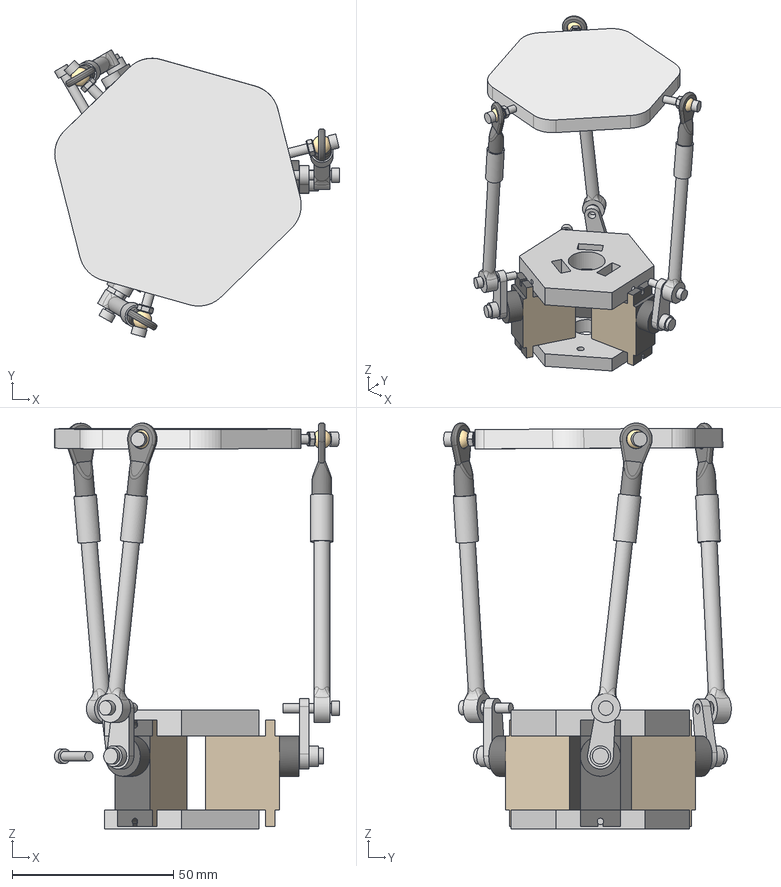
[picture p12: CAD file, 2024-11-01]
STEWIE.step
88.5 x 89.3 x 126.0 mm
Link 2 x 3
Link 1 x 3
BALL JOINT 3MM BOLT x 6
Ball x 3
nut x 3
base plate
plate2
Top Plate
NEW MOTOR x 3
2.5 M * 7 H x 3
